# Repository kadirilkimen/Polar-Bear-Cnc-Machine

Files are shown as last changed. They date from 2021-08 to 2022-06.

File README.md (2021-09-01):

# the PolarBear
http://www.kadirilkimen.com/thepolarbear

# Bom of the prototype is uploaded.

## Please read the description below. It is important.
## It is not the BOM of Version1.

## BOM is only for the basic machine prototype.
> printbed, rotary table surface and toolheads are not included to this BOM.

I'm still working on version1.

I received a lot of requests for the BOM and decided to upload the BOM of the prototype.

Please use this as a reference and build the machine for familiarization only or practice before building v1.

You may experience some problems during installation and/or use. But none of them are unsolvable.

#### Have fun!

I will update the polarToolsJs to work with both rotary axis and cross slide axis in a week. If you build the machine, you will need it to convert a regular g-code to the PolarBear compatible format.

I will also upload a simple assembling instructions in a week.

polarToolsJs repository : https://github.com/kadirilkimen/polarToolsJS

>
> ### IMPORTANT
> #### All existing STL files and the design of the machine are still in development.
> Some parts will be updated for better printing and easier assembly.
>
>

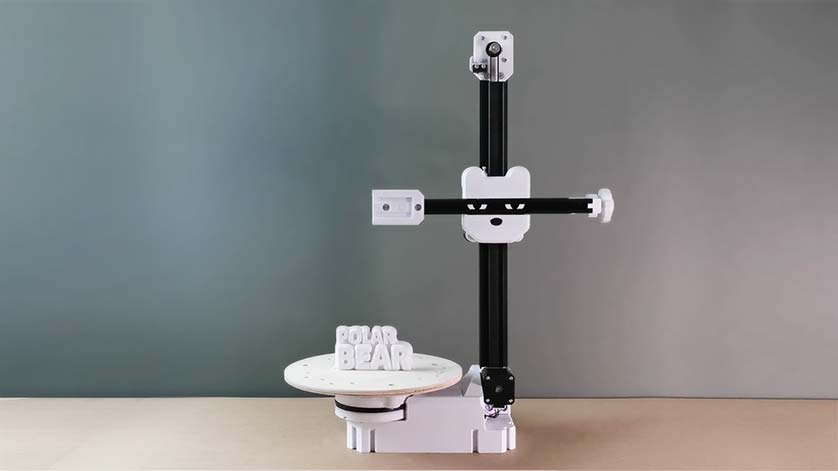
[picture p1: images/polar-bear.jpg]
PolarBear CNC Machine PolarBear


the PolarBear needs support. I would appreciate any contribution to help with funding.
I will add any supporter's name/logo into the CREDITS documentation both in this repository and the website :
http://www.kadirilkimen.com/thepolarbear

## It is a multi-purpose CNC machine

* What is it?
  * It can be a 3d printer, a CNC milling machine, or whatever you think it can do.
  * It is not designed to be a complete replacement for existing machines.
  * It has different pros that other machines don't have.

* Some pros of other machines
  * A Cartesian 3d printer is vastly available and easy to access. Software works well with them.
  * A CNC router is good for working on large sheet materials.
  * A plotter/cutter machine is good and fast for drawing/cutting paper and foil.
  * Stock materials are mostly rectangular.

* Some pros of the PolarBear
  * In most cases it can work faster.
  * The rotary axis makes it possible to work on different surfaces of the workpiece, rather than just vertical ones.
  * It could easily have another function. It only takes a minute to switch between CNC milling and 3d printing.
  * Due to the different kinematics of the PolarBear, it moves more smoothly, which increases the precision and quality of the work.

## Main Goals

### Improving mechanical design

The current prototype works as expected. But some improvements are needed.

### Improving rigidity

The current design is rigid enough for most jobs. 3d printing, pens, wood burning works just fine without any flexing.

CNC milling is also good, but requires more rigid mechanics to get better.

### Making mechanical calibration easier

I need to improve the design to eliminate two calibration issues.

* I need to make it easy to align the tooltip to the absolute center of the rotary axis.

* I should make it easy to adjust the squareness of the vertical mast and the rotary axis.

### Making a scalable design

* Making a scalable design so that people can build the PolarBear in different sizes.

* I'm thinking to develop a laser cut sheet metal body version so people can build robust industrial machines of any size.

### A Custom Firmware

#### Do we need a custom firmware?

The current prototype runs on an off-the-shelf 3d printer controller with a Marlin based firmware. I've also done tons of experiments with an Arduino/Grbl CNC shield.
It just works great. However, since these off-the-shelf components and firmware don't know the PolarBear kinematics, I had to develop a postprocessor for g-codes:

https://github.com/kadirilkimen/polarToolsJS

This postprocessor imitates the polar movements that would be run by a cartesian controller. This works great too. But it is not efficient.
It generates twice or more g-codes and it cannot run the machine at efficient feed rates. Even if we calculate the best feed rates, the firmware will treat the movements as cartesian and recalculate the decelerations and accelerations, which would be wrong for polar motions.

Therefore, without special firmware for polar and cross slide motion, the machine often runs at inefficient feed rates.
Feed rates are still good. It's not just the best. So if you're looking for a quick, simple and good enough solution, an off-the-shelf controller is for you.

I am thinking to modify Grbl. It seems simpler to accomplish. Also, I'm sure a lot of people will use Grbl controller. Because it is very affordable and simple.
For more complicated firmware and controllers, I will need help.
When I develop Grbl based firmware for the PolarBear, it would become a blueprint for other developers and they can add kinematics to other firmware.

Current controller boards are good. However, in order to make them compatible with the quick-change tool adapter, people need to make modifications.
Which is not for everyone.

So the ultimate solution is to develop a custom controller board and custom firmware.
Fortunately, we don't have to invent them from scratch. There are some great open source projects to start with.

After all, the absence of a dedicated controller and firmware is not a bottleneck for the project.

### A Custom Cam software

#### Do we need a custom cam software?

Unfortunately, when it comes to a "cam software", I don't think there is a good open source solution. All they have flaws or lack of enough skills.
If I were to cite open source software as a successful "cam software", it would be Cura. Although it is a cam software, it is only for 3d printing.
There are good freeish cam softwares out there. However, they lack sufficient features or often push you to purchase services or subscriptions.
I think there is a lack of good open source CAM software in the world right now.
When I want to do a CNC related project, the lack of good open source cam software limits me a lot.
Often I have to solve the problem using zillions of apps and libraries. If I couldn't code, it would mostly be impossible.

There are people who do not code, have ideas and need cnc machines. It's time to fix this problem.

So an open source cam software is a must to develop.

It's not an issue directly related to the PolarBear project, but a good cam software familiar with the PolarBear will increase the efficiency of the machine.

### Universal Quick Change Tool adapter with an electronic interface

#### Why?

All 3d printers, CNC routers, CNC milling machines, plotters (... and tons of other stuff) are all CNC machines.

The difference between these machines is their functionality and construction.
Although all these machines can be modified to do the work of others, they cannot be efficient at functions they were not designed to do.
Because all different functions require different mechanical capacities and speeds.

Thanks to the PolarBear's unique design and kinematics, the limits between the needs of the different functions are more blurred.
While it can be as fast as a 3d printer, it can be rigid for use as a CNC milling machine as well.

The only clear limit is the PolarBear's work volume.

So why not use it as a multi-purpose machine?

## Funding the project

It takes full-time effort of more than one person to design a good machine and a good cam software.

Right now I'm funding and working on it just myself.

I look forward to more support and donations to go further and build a business around it.

With some support, I'll be able to finish the scalable mechanical design and start selling kits.

Then I think selling kits will finance the project and I will be able to focus on developing open source powerful cam software.

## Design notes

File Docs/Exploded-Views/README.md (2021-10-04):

## Important ##
### These exploded views may not contain all required elements ###

Since the polarBear is still a prototype, I don't have any instructions or documentation for assembly.

If you are building the prototype version, these exploded views may help you to assemble it.

I am already working on version 1. Once the V1 is ready, I will publish documents, instructions and videos.

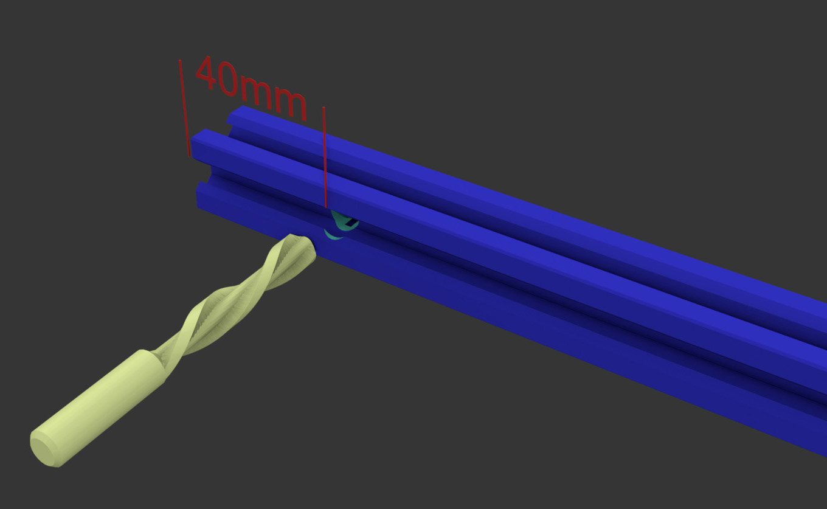
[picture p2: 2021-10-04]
Docs/Exploded-Views/X-axis/x-axis-1.jpg

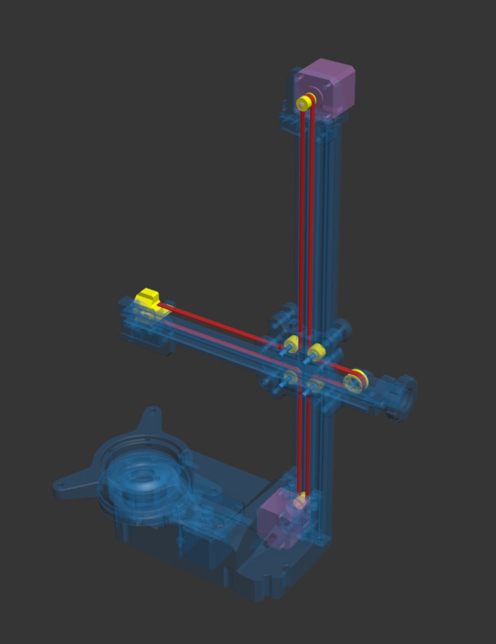
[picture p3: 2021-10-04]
Docs/Exploded-Views/Belt/belt-1.jpg

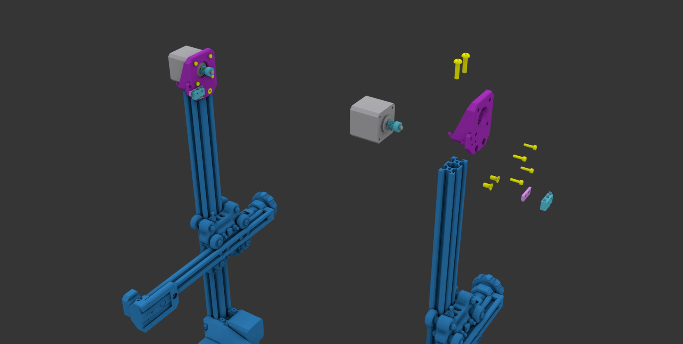
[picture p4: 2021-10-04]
Docs/Exploded-Views/Z-motor/z-motor-1.jpg

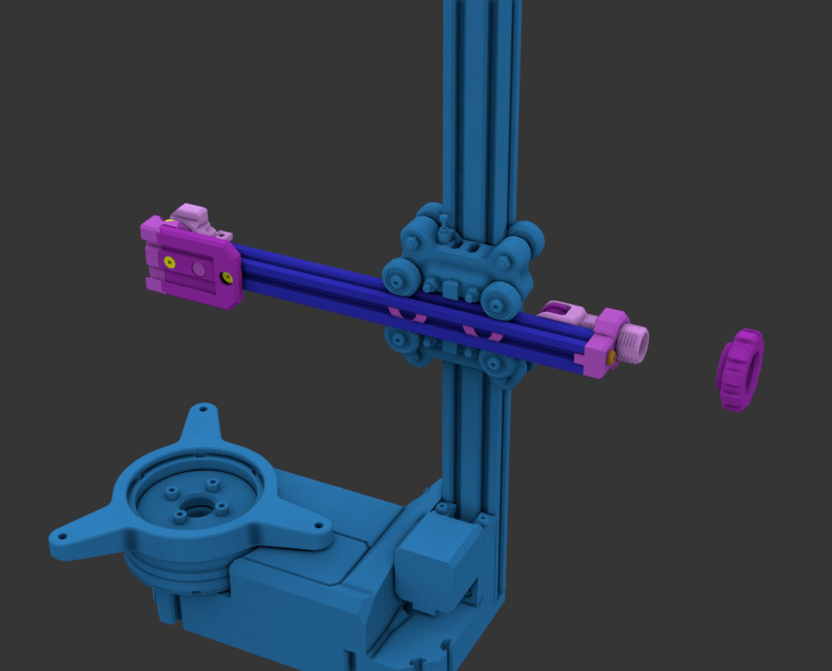
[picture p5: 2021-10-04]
Docs/Exploded-Views/X-axis/x-axis-8.jpg

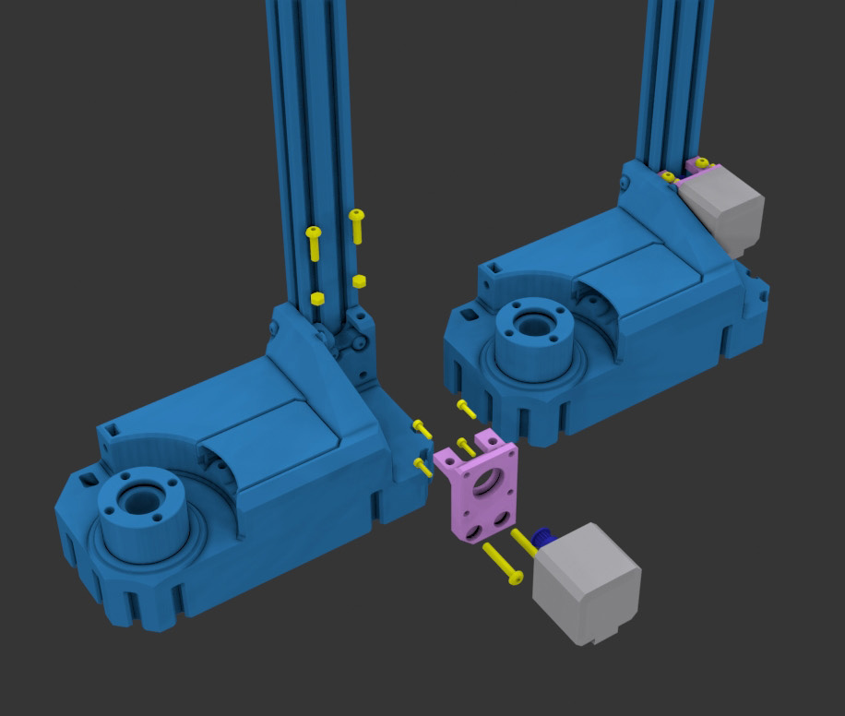
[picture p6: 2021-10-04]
Docs/Exploded-Views/X-motor/x-motor-1.jpg

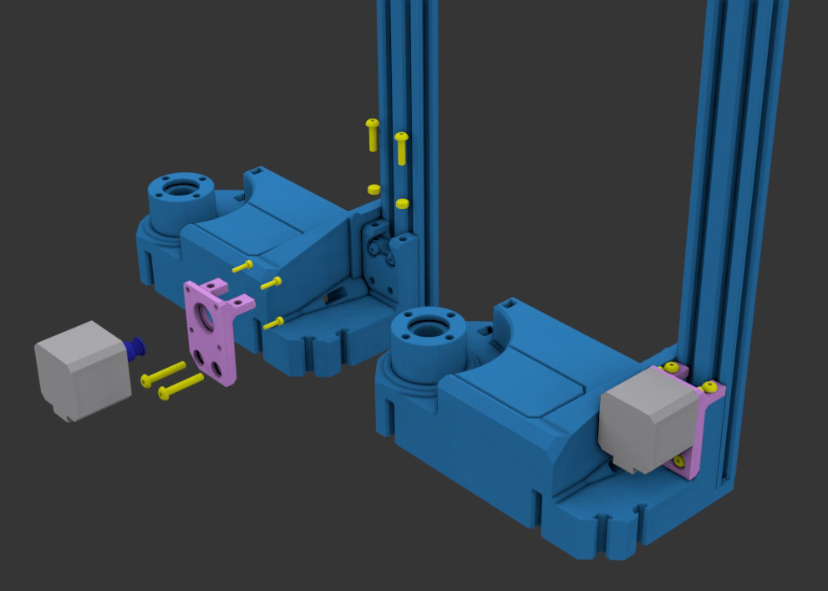
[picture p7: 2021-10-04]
Docs/Exploded-Views/X-motor/x-motor-2.jpg

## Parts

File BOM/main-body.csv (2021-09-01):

Item | Quantity | Size/model | Source | Description
Read the description > |  |  |  | Please keep in mind, Main body design will be different in version 1. It seems I designed the x motor mount poorly. It makes the assembling vertical 2040 extrusion very difficult. Two t-slot nut become unaccesible while assembling. I had to tape the t-nuts on the place before assembling it.
Main-body | 1 |  | STLs/main-body/main-body.stl | The Squareness of this part affects the overall squareness of the machine. So it is important that your printer must be squared and calibrated carefully. It takes time but its worth to print slow.
Rotary-motor-cover | 1 |  | STLs/main-body/rotary-motor-cover.stl | Least important part. Just a cover
X-motor-mount | 1 |  | STLs/main-body/x-motor-mount.stl | Design of this part makes the assembly of the vertical 2040 extrusion very difficult. It’s design will be changed completely on v1.
Z-motor-mount |  |  | STLs/main-body/z-motor-mount.stl
2040 V-slot extrusion | 1 | 500mm |  | Longer than 500mm Z axis is not much practical for a 3d printed body machine.
M5 socket cap bolt | 2 | 50mm |  | For the rotary axis belt tensioner idlers.
M5 nylon nut | 2 |  |  | For the rotary axis belt tensioner idlers.
625 bearing | 4 | zz or 2rs |  | I used bearings as belt idlers. You can use bearings or off the shelf idlers.
M5 round socket cap bolt | 9 | 20mm |  | to fix 2040 extrusion to the body and x motor mount
M5 round socket cap bolt | 2 | 30mm |  | to fix x motor mount to 2040 extrusion thru the main body
M5 T-nut ( vslot nut? ) | 9 |  |  | to fix 2040 extrusion to the body and x motor mount
M5 nut | 2 |  |  | to fix x motor mount to main body
M5 round socket cap bolt | 2 | 20mm |  | to fix z motor mount to main body
M5 countersunk socket cap bolt | 2 | 10mm |  | to fix z motor mount to main body

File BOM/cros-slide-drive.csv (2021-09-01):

Item | Quantity | Size/model | Source | Description
Read the description >
Nema17 stepper | 2 | 4401 |  | X and Z motors
GT2 16T pulley | 2 | 16T |  | Teeth count is important for an accurate positioning. All the documentation will assume that you use 16T pulley for the cross slide steppers
M3 socket cap screw | 8 | 10mm |  | to fix X and Z steppers to the motor mounts
GT2 open end belt with 6mm width | 1 | 1500 |  | cross slide drive belt
V4 limit switch | 1 |  |  | Z axis limit switch
M2 self tapping screw | 2 | 12 – 16mm |  | for the limit switch
2 core wire for the limit switch | 1 | ~1000mm
Nema 17 stepper motor cable | 2 | ~1000mm

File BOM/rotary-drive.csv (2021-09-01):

Item | Quantity | Size/model | Source | Description
Read the description >
Nema17 stepper | 1 | 4401
GT2 16T pulley | 1 | 16T |  | Teeth count is important for an accurate positioning. All the documentation will assume that you use 16T pulley for the rotary axis stepper
M3 socket cap screw | 4 | 10mm |  | to fix rotary axis stepper to the main body
M3 washers | 4 |  |  | to fix rotary axis stepper to the main body
GT2 400mm loop belt with 6mm width | 1 | 400mm
Nema 17 stepper cable | 1 | ~1000mm

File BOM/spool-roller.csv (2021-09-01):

Item | Quantity | Size/model | Source | Description
Read the description > |  |  |  | When I was prototyping PolarBear, I needed a spool roller and designed it right away. Requires improvements. It needs weight or friction to stay on the ground. When the spool becomes lighter it starts to move or the spool is pulled out by the extruder. But still usable
Spool-bar | 4 |  | STLs/accesories/spool-bar.stl | 3d printed part
6001 bearing | 4 | 6001 |  | I designed the spool roller for the 6001 bearing because it was a prototype and I already had spare 6001 bearings.
M5 screw | 4 | 20/30mm |  | I usually cut threads on printed parts using tap tools when the part is not structural. So, the holes on the spool-bar.stl are smaller than M5 size. Use M5 tap to cut thread or use a 5mm drill to enlarge the holes. 20Mm for threaded 3d print part and 30mm for nuts
M5 nut(optional) | 4 |  |  | If you don’t want to cut threads on the 3d printed parts, simply use longer screw and use nuts to fasten parts

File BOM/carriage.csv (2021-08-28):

Item | Quantity | Size/model | Source | Description
Read the description > |  |  |  | Carriage contains 4 set of idlers inside. I used a pair of 625 bearings for each idler set. Since they don’t have flange to guide belt, belt plays around and cause alignment issues. Carriage block design will be changed in v1
carriage | 1 |  | STLs/carriage/carriage.stl | This part must be as rigid as possible. Use high top/bottom and wall thickness. Infill is important but thicker outer shel is more important for rigidity. I used 1.6mm outer shell and %20 cubic infill. I print with 0.4mm nozzle and infill is better when I set 0.6mm line width for infills.
decoration parts | 1 set |  | STLs/carriage/decorations/ all models | bear eyes designed to slide in x axis extrusion. Others are designed to snap-in carriage block. Print as light as possible.
24mm v-slot wheels | 8
M5 round socket cap bolts or M5 low profile socket bolts | 8 | 40mm |  | For the v-slot wheels. Use at lease 10.9 grade bolts. I use round socket cap bolts for the wheels because I buy bolts in bulk from my local sources and they don’t have low profile bolts.
M5 nylon nut | 8 |  |  | For the v-slot wheels
6mm v-slot spacer | 4 |  |  | For the v-slot wheels
6mm v-slot eccentric spacer | 4 |  |  | For the v-slot wheels
M5 round socket cap bolts or M5 low profile socket bolts | 4 | 30mm |  | for the idlers in the carriage
M5 nylon nut | 4 |  |  | for the idlers in the carriage
M5 washer | 4 |  |  | for the idlers in the carriage
625 bearing | 8 | zz or 2rs |  | for the idlers in the carriage
M3 socket head cap bolt | 2 | 20mm |  | for the limit switch adjusters. You need M3 tap to install this bolts to the place.
M3 nut | 2 |  |  | for the limit switch adjusters

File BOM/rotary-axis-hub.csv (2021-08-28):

Item | Quantity | Size/model | Source | Description
Read the description > |  |  |  | This is the first prototype of the rotary axis hub. I've already made heavy changes and version 1 will have a different rotary axis design than this. Currently, a surface for bearings needs to be printed with support and is not clearly printed. Finally affects the precision and straightness of the rotary axis
Rotary-axis-body | 1 |  | STLs/rotary-axis-hub/rotary-axis-body.stl | This is the most important part of the printer. It should be printed as accurately as possible. Therefore, do not print fast and be sure to calibrate the flow rate before printing this part.
Rotary-axis-preloader | 1 |  | STLs/rotary-axis-hub/rotary-axis-preloader.stl | This part is used for preloading the rotary axis body bearings. Preloading is very important process. This part also important. Do not print fast and be sure to calibrate the flow rate before printing this part.
M5 socket cap bolt | 4 | 60mm |  | It can be any type of screws. Prefer 10.9 grade bolts if you can find.
M5 nylon nut | 4
16010 bearing | 2 | ZZ or 2RS |  | Bearing selection can be confusing.I used 3EUR/piece bearings for the prototype. I wouldn’t recommend buying very high quality bearings. Cost of the bearing is more likely affects it’s load bearing and speed capabilities more than its precision. Ah, also don’t buy deadly cheap carbon steel bearings. A real bearing must be made from bearing steels.

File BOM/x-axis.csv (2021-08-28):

Item | Quantity | Size/model | Source | Description
Read the description > |  |  |  | Almost all 3D print parts on the x axis will change on the version 1. Current parts are working fine. But the belt’s position will change and it requires to redesign all related parts. Also some parts require too much post work, which is not nice and they needed to be re-designed.
Belt-end-clamp | 1 |  | STLs/x-axis/belt-end-clamp.stl | This part designed on the way. It’s not intended to be a final design part.
tool-adapter-cap | 1 |  | STLs/x-axis/tool-adapter/tool-adapter-cap.stl | This part designed on the way. It’s not intended to be a final design part.
tool-adapter-body | 1 |  | STLs/x-axis/tool-adapter/tool-adapter-body.stl | This part must be as accurate as possible. Print it slow with 0.1mm layer height
tool-plug-template | 1 |  | STLs/x-axis/tool-adapter/tool-plug-template.stl | Don’t print this model right away. Instead use it to design your own tool holder
Tool-adapter-t-nut-brick | 1 |  | STLs/x-axis/tool-adapter/tool-adapter-t-nut-brick.stl | This is an M3 nut wrap that prevents the nut from rotating freely.
tool-locking-shoe | 1 |  | STLs/x-axis/tool-adapter/tool-locking-shoe.stl | This part applies force to the tool plug to keep it pressed to the Socket. It does it’s job perfectly. But it’s design is not good and it stucks in position. It changed on v1.
M3 socket cap bolt | 1 | 20mm |  | to secure the tool holder
M3 nut | 1 |  |  | to secure the tool holder
M5 socket cap bolt | 2 | 10mm |  | to fix tool adapter cap to the x-axis extrusion
M5 t-slot nut | 2 |  |  | to fix tool adapter cap to the x-axis extrusion
M5 countersunk socket bolt | 2 | 10mm |  | to fix tool adapter body to the x-axis-extrusion
M5 t-slot nut | 2 |  |  | to fix tool adapter body to the x-axis-extrusion
M5 round socket cap bolt | 1 | 20mm |  | to fix belt end clamp to the x-axis-extrusion
M5 t-slot nut | 1 |  |  | to fix belt end clamp to the x-axis-extrusion
V4 limit switch | 1 |  |  | x axis limit switch
M2 self tapping screw | 2 |  |  | for the limit switch
2 core wire for the limit switch | 1 | ~1500mm
belt-tensioner-guide-cap | 1 |  | STLs/x-axis/belt-tensioner-guide-cap.stl
belt-tensioner-knob | 1 |  | STLs/x-axis/belt-tensioner-knob.stl | It’s has a CCW direction thread.
belt-tensioner-screw | 1 |  | STLs/x-axis/belt-tensioner-screw.stl | It’s has a CCW direction thread.
cross-drive-idler-pulley | 1 |  | STLs/x-axis/cross-drive-idler-pulley.stl
M5 round socket cap bolt | 1 | 20mm |  | to fix belt-tensioner-guide-cap
M5 socket cap bolt | 1 | 30mm |  | to fix belt tensioner pulley
M5 t-slot nut | 1 |  |  | to fix belt tensioner pulley
M5 washer | 2 |  |  | to fix belt tensioner pulley
625 bearing | 2 | zz or 2rs |  | Cross-drive-idler-pulley bearings
2020 v-slot extrusion | 1 | 300mm |  | X-axis rail

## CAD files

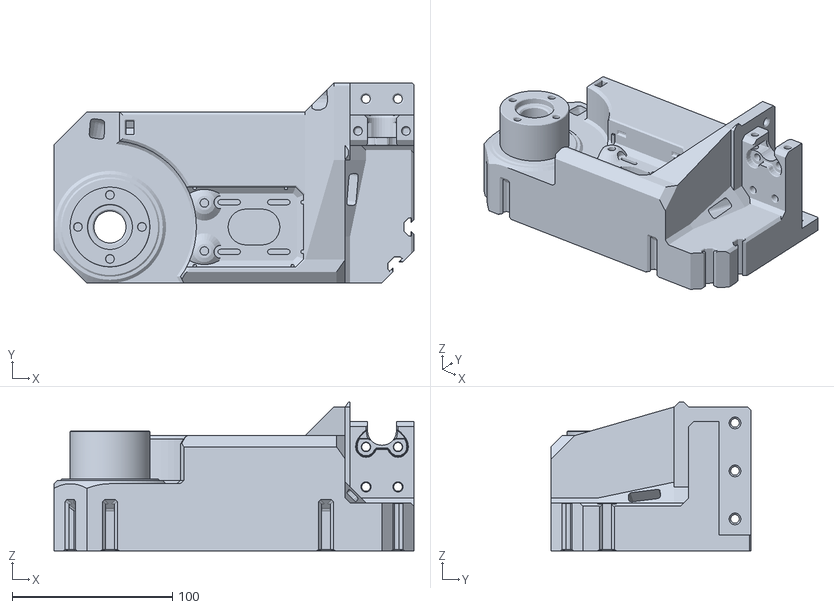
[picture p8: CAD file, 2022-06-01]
STLs/main-body/main-body-without-support.stl
225.0 x 125.0 x 93.0

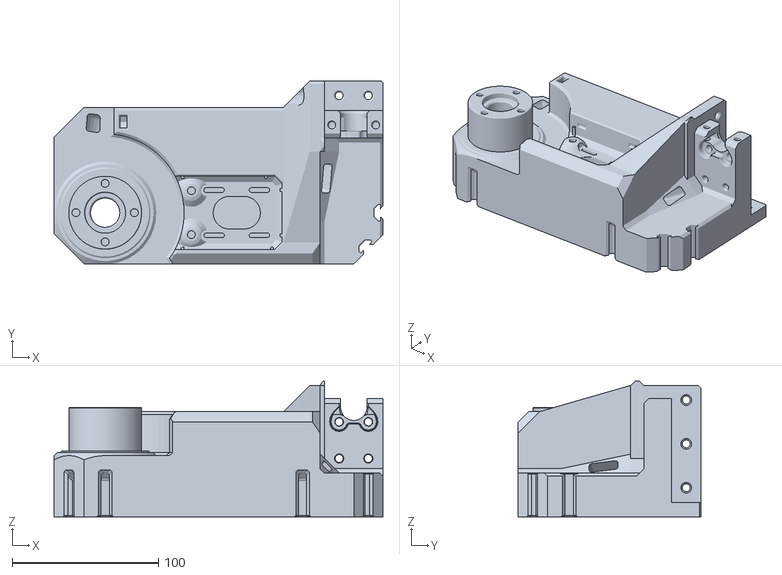
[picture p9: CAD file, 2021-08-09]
STLs/main-body/main-body.stl
225.0 x 125.0 x 93.0

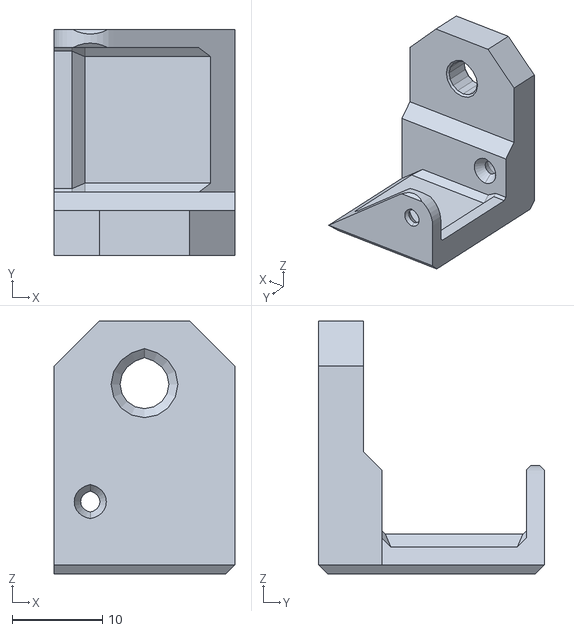
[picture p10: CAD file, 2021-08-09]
STLs/accessories/drag-chain/drag-chain-mast-mount.stl
20.0 x 25.0 x 28.0

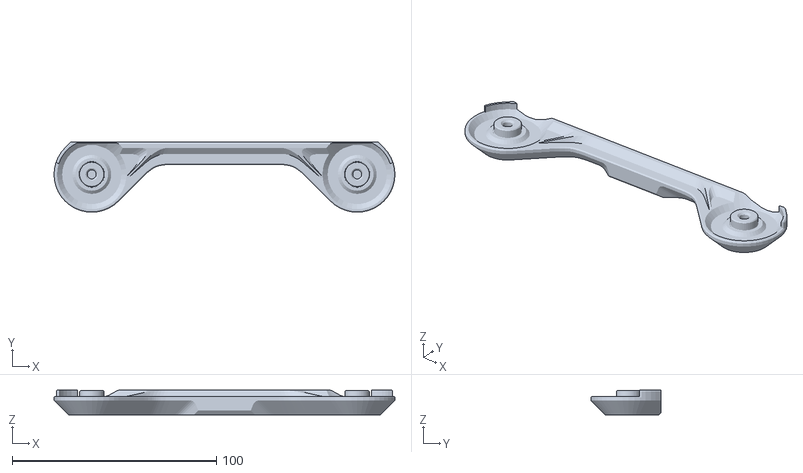
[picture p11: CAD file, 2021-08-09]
STLs/accessories/spool-bar-6001.stl
167.0 x 34.5 x 12.0

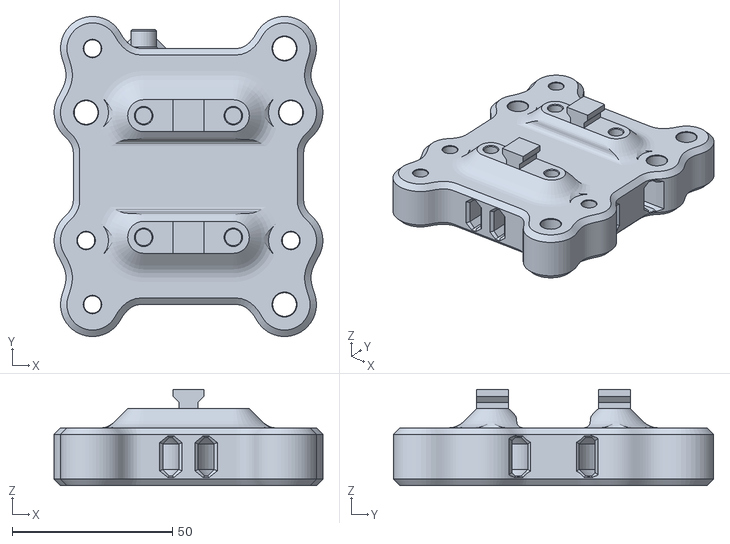
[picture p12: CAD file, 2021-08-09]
STLs/carriage/carriage.stl
84.0 x 100.0 x 30.0

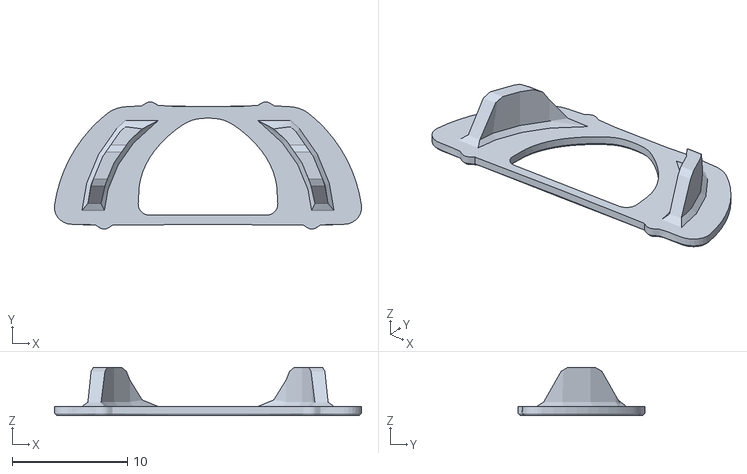
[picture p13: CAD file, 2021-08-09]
STLs/carriage/decoration/bear-eyes.stl
26.6 x 11.0 x 4.20

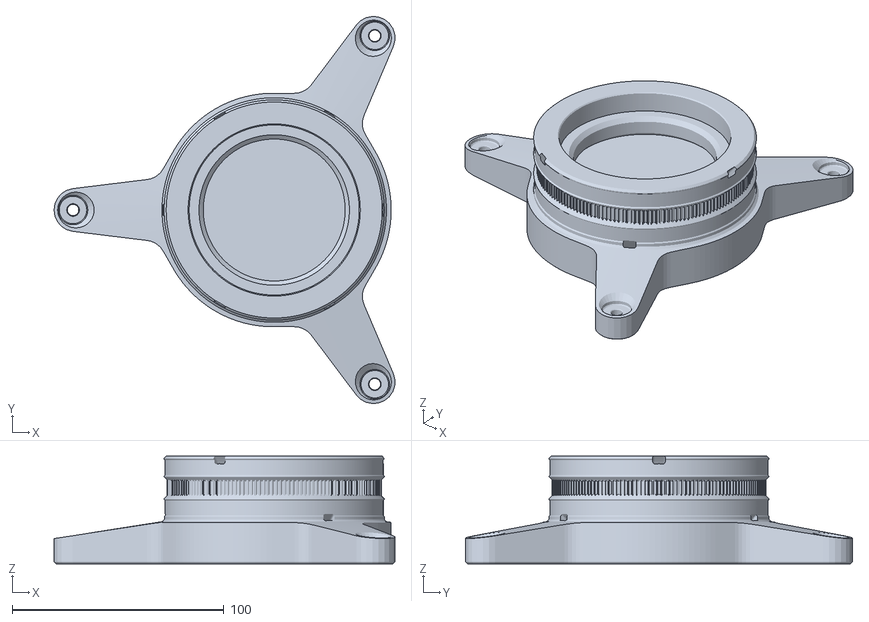
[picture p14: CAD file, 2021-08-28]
STLs/rotary-axis-hub/rotary-axis-body-without-builtin-supports.stl
161.0 x 182.8 x 51.0

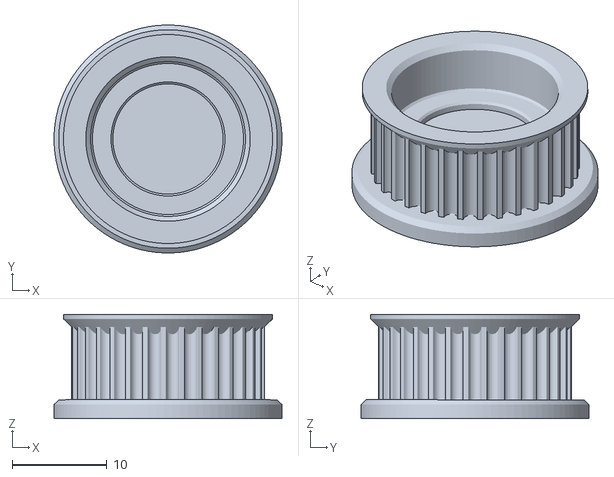
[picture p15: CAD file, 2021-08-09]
STLs/x-axis/cross-drive-idler-pulley.stl
24.0 x 24.0 x 11.0

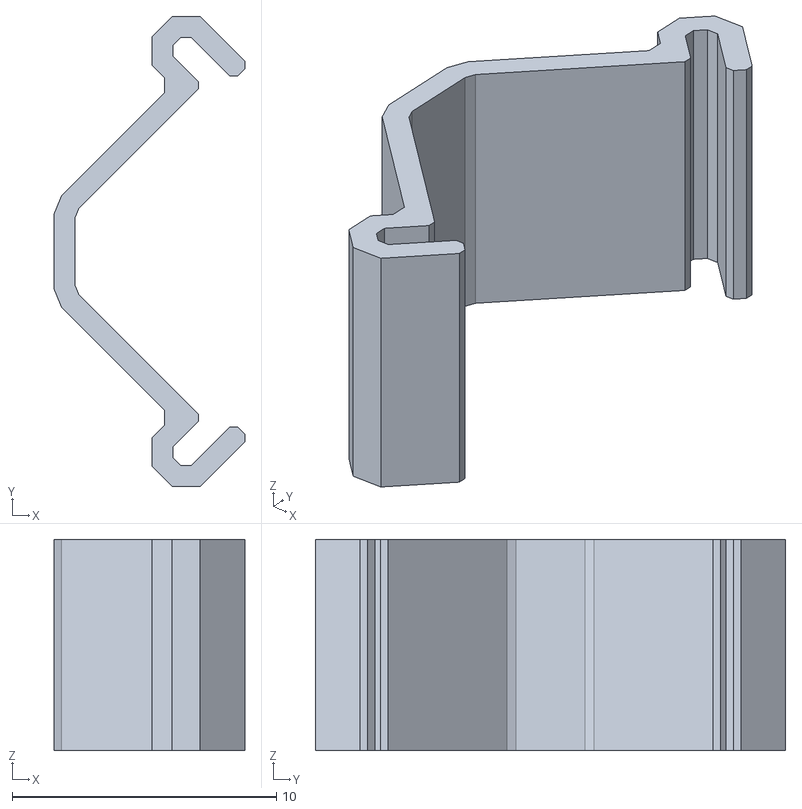
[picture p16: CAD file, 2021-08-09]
STLs/accessories/drag-chain/drag-chain-link-lock.stl
7.22 x 17.8 x 8.00

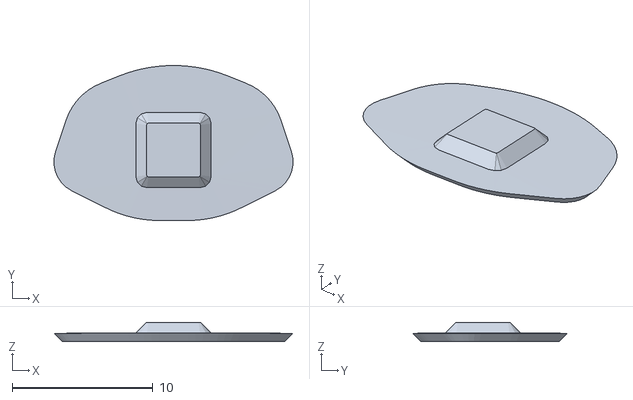
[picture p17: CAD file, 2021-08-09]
STLs/carriage/decoration/bear-nose-cap.stl
17.0 x 11.0 x 1.38

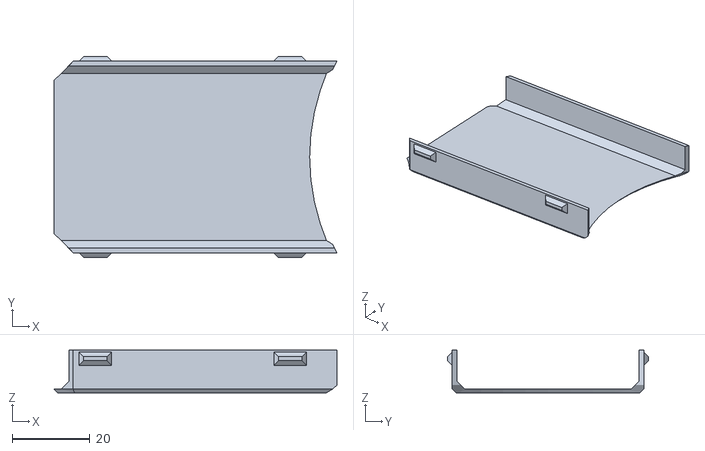
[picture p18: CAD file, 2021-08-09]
STLs/main-body/rotary-motor-cover.stl
72.6 x 51.6 x 11.0

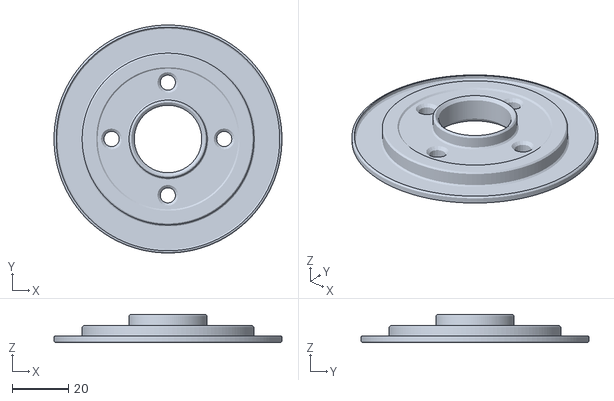
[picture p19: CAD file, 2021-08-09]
STLs/rotary-axis-hub/rotary-axis-preloader.stl
80.9 x 80.9 x 10.00

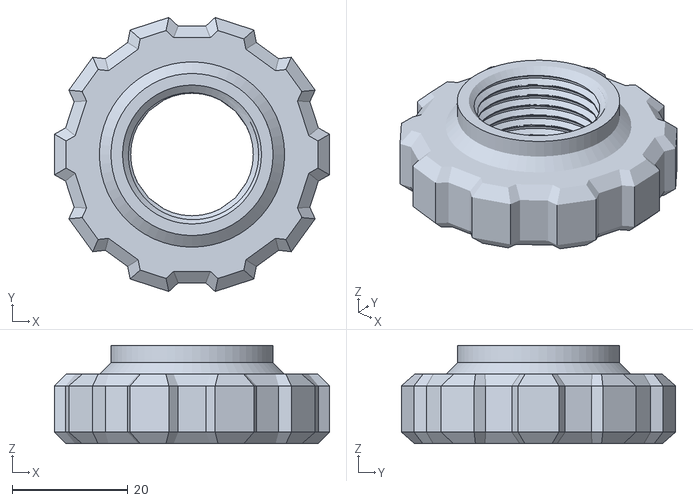
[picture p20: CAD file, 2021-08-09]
STLs/x-axis/belt-tensioner-knob.stl
47.5 x 47.4 x 17.0

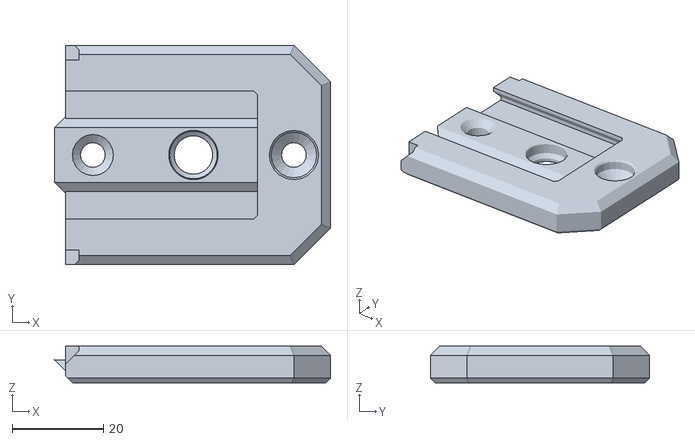
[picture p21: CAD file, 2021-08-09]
STLs/x-axis/tool-adapter/tool-adapter-body.stl
60.4 x 48.0 x 8.00

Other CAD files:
STLs/accessories/drag-chain/drag-chain-x-mount.stl
STLs/carriage/decoration/bear-head-top.stl
STLs/rotary-axis-hub/rotary-axis-body.stl
STLs/x-axis/tool-adapter/tool-adapter-cap.stl
STLs/accessories/drag-chain/drag-chain-link-body.stl
STLs/carriage/decoration/bear-head-bottom.stl
STLs/main-body/x-motor-mount.stl
STLs/main-body/z-motor-mount.stl
STLs/x-axis/belt-end-clamp.stl
STLs/x-axis/belt-tensioner-guide-cap.stl
STLs/x-axis/belt-tensioner-screw.stl
STLs/x-axis/tool-adapter/tool-adapter-t-nut-brick.stl
STLs/x-axis/tool-adapter/tool-locking-shoe.stl
STLs/x-axis/tool-adapter/tool-plug-template.stl

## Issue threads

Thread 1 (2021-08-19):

Questions

HumanG33k, 2021-08-19:
Project look cool.

How easy is to build my own prototype ?
There is somewhere a tutorial for that ?

kadirilkimen, 2021-08-19:
Hi,
Thanks.
It requires some basic skills;
1 - You should be able to use basic tools.
2 - You must have basic electrical knowledge.

Then, if you have all the printed parts and all the required items in the BOM list, it should take about 1 hour to assemble.

I'm still improving the mechanical design at the moment. Therefore, I have not shared a BOM list and a tutorial.

When I'm done with the design, I'll post a few videos, including an assembly tutorial, along with the new STLs and BOM list.

HumanG33k, 2021-08-29:
Thx when you say basic electrical knowledge. I guess making arduino stuff or home electricity is enough ?

I will share your project around me (some hacker space & community )
Maybe you can create a list of people/organisation using your product and ready to product/ship by country.

kadirilkimen, 2021-08-29:
Having some arduino knowledge would make it very easy.
It requires some wiring and you may or may not need soldering, depends on how you get required wires.
Also power supply may or may not require some A.C. wiring. It depends on what kind of power supply you will use.

If you familiar with arduino and if you can work safely with A.C. you can build the machine easily. If you buy a ready to use wired power supply, then you don't need to deal with A.C. and some arduino or similiar wiring knowledge is enough.

You are welcome to use/share my digital media and the project by respecting the conditions below;
 - Use them as is. Don't change the content.
 - Make sure that a proper attribution is available with the content.
Feel free to share anywhere.

I am thinking to develop a portal like website for the project. Where people can share their polarbear experience and ask questions etc.

Thanks alot!

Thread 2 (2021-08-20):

Conventional mill design with rotary table without Y axis

Vorlent, 2021-08-20:
Start with a conventional mill and remove the Y axis. Add the rotary table on top of an X axis.

One big problem with this idea is that the spindle has to align with the center of the rotary table on the Y axis which was removed in this design. On the plus side the rotary table allows you to get to the other side meaning that no space is wasted on where the Y axis would be. If the design is still lacking in rigidity you could use a design similar to a CNC router with basically a column on both sides.

[Sketch](https://i.imgur.com/OKNSXip.png)

The head can be tilted 90°.

Disclaimer: I haven't touched or built a CNC machine in real life.

kadirilkimen, 2021-08-20:
Your suggestions do not improve PolarBear. It makes it a different design.
It also takes away some pros of the Polar Bear.

Current design is simple.  It requires less materials to build and has some pros compared to other kind of desktop machine concepts.

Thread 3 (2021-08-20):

Materials

alak, 2021-08-20:
Hi,

First of all, thanks for your work on this project.
What kind of material the CNC work with ?

Thanks

kadirilkimen, 2021-08-20:
Hi,
Thanks.
It can work on wood and softer materials.
I carved some woods while developing the first prototype. Unfortunately I couldn't film them. I will demonstrate some wood work with version 1 release.

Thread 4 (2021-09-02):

Support

Alvarito414, 2021-09-02:
Hi! Will you add a list of specific recomemded components for people with not so advanced knowledge on arduino and coding but would still want the machine since it is a great concept and seems promising? Also are you able to give some kind of estimate of time until v1 of the PolarBear is ready?

As a suggestion for future versions, i think the machine cant get to every single spot when sculpting but it can defenetly do lots and more than a normal cnc machine. I think that if you added a y axis that carried the rotating base it would be the perfect machine but i know that this is a lot to ask and having a bit of 3d modelling experience myself i know it is extremley difficult to do too while also keeping the machine compact and stable. Again, i think this would start to get out of the initial concept and that if it was considered, it would have to form part of future versions. I hope to get a response and to see further development of the machine.
Thanks!

kadirilkimen, 2021-09-02:
Hi!
Current STLs and BOM is only for experimental purposes and I am working on V1.
Once I release v1, I will also publish several building videos, instructions and tutorials. Unfortunately releasing time of the v1 is currently unclear. I am waiting some deliveries from china and other places. So far, statuses of some some shipments are unclear.
It happened before. I had to wait more than extra 2 months for deliveries of the current prototype.
So, I was expecting the deliveries one week ago. From this point, I can say that releasing the v1 would take 1.5 months.

You are right. Adding another axis definitely would increase it's machining capacity. But again you are right, it adds extra complexity. Its quite possible to make this machine 5 axis. But, there is no easy firmware and cam software solutions. Without a complete toolchain it is not something worth to spend energy. May be in the future.

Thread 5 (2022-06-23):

Consider Duet3D/Klipper instead of custom firmware

stisa, 2022-06-23:
Instead of developing your own firmware, consider adding a new kinematics to some common firmware.
For example, duet already supports polar kinematics and corex/hbot, so you could probably find a way to generalize the existing polar to a XZ kinematics other than cartesian by adapting `MotorStepsToCartesian` and `CartesianToMotorSteps` (your is a T-bot I think?)

Ref:
https://github.com/Duet3D/RepRapFirmware/wiki/Adding-New-Kinematics
https://github.com/Duet3D/RepRapFirmware/blob/3.4-dev/src/Movement/Kinematics/CoreKinematics.cpp
https://github.com/Duet3D/RepRapFirmware/blob/3.4-dev/src/Movement/Kinematics/PolarKinematics.cpp
https://github.com/Duet3D/RepRapFirmware/blob/0b75dea11109f4734df3aad06c09a868e55b5332/src/Movement/Kinematics/PolarKinematics.cpp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

kadirilkimen, 2022-06-23:
Hi,
I am not developing a firmware for the PolarBear. There is no need to develop something from scratch. I just developed a cartesian to polar post processor, which is not a firmware. It Just polarizes gcodes.

I am very into klipper firmware. I am thinking to work on it.

However, I designed thr PolarBear as flexible as I can. There is no restriction for the firmware. I decided to do it that way, because people would build machines for different purposes. Most comments I got were about cake printing or ceramic printing bots. Therefore, they can even use simplest arduino grbl to drive the machine.

The babyBear project is going to be on github in july. It is based on mks robin nano 3 board and I will release both marlin and klipper configurations for it.

kadirilkimen, 2022-06-23:
I am happy to hear that another build is on the way!

In my opinion, knowledge should be all open source. I use open source information almost everyday both for business and life. I had to make it open source 😊

Quick change tool holder needs some improvements in future. But current one still good enough. I will be more happy when people build interesting tools 😊

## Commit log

2021-08-09 Update STLs
    [bear-eyes.stl, bear-head-bottom.stl, bear-head-top.stl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]
2021-08-28 BOM of the prototype uploaded
    [carriage.csv, cros-slide-drive.csv, main-body.csv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]
2021-09-01 main-body BOM updated
    [main-body.csv, spool-roller.csv]
2021-09-01 2040 extrusion added
    [main-body.csv]
2021-09-01 Updated stepper cables
    [cros-slide-drive.csv, rotary-drive.csv]
